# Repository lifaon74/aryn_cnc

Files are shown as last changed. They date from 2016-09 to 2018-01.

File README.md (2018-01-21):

# Aryn CNC

Aryn CNC is a personal project of building a CNC machine for 3D printing, carving, or PCB drilling.
The final should result in a low cost "professional" CNC tool able to work in 50cm x 50cm x 40cm volume (X, Y, Z).

<!---<a href="./main.jpg"><img src="./main.jpg" height="500"></a>-->
Aryn CNC 01 (http://www.youtube.com/watch?v=Y5BFLhbk83g "Aryn CNC 01")

## The goals
* **modular** : easy to add, remove and update parts => it's for me the most important goal.
* **professional** : fast, precise and strong, that's why I chose to use only high quality materials. It increase the price, but he, we want the best no ?
* **'low' cost** : far under the professional market (price estimated around 500$, expensive but not as much as a pro solution). I'm expecting same or better precision.
* **important work volume** : 50cm x 50cm x 40cm (aprox) into a 70cm side cube (you should be able to put it in your car). It's a far better ratio than most of the 3D printer (ex: [Haeckel](http://reprap.org/wiki/Haeckel) 47cm x 47cm x 57cm size for a 20cm x 20cm x 35cm print volume)
* **for makers** : if you have time, are handyman, own a 3D printer (or know someone) and like precision, this CNC is done for you.

## Before your start
* Take care to work as much precise as possible.
* Most of the parts are not available into generic DIY store, you'll need to order them online and/or contact peoples.
* You'll need a **shitload** of screws, nuts and washer : buy them into big pack (1000pcs) and keep them for future projects.
* You'll need a complete set of tools.
* Take care to have enough place (70cm side is big !).

## My Setups
Prusa i3
* 0.2mm layer height
* 30% infill, 50% for some parts which need solidity
* PLA (black, red, and maybe orange)

## Table of Content
1. [x] [Frame](./documentation/frame/frame.md)
2. [x] Axis
	* [x] [X](./documentation/x_axis/x_axis.md)
	* [x] [Y](./documentation/y_axis/y_axis.md)
	* [x] [Z](./documentation/z_axis/z_axis.md) - TODO : plate

3. [x] Tools
	* [x] Extruder
    * [Diamond Head](./documentation/tools/extruder/diamond_head/diamond_head.md) - (in experiment)
	* [x] [Milling](./documentation/tools/milling/milling.md) - (in experiment)

4. [x] Electronic
	* [x] [Power supply](./documentation/power_supply/power_supply.md)
	* [ ] Wiring - TODO
	* [ ] Program and drivers - TODO

**The project is still in progress, some parts may change and it's not my full time job (don't expect it will be finished too fast). This git is here to share my work. Fell free to test, contribute, improve or comment (create issues for that).**

If you want to support the project: 



hit counter

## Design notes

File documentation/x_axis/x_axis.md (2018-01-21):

# X Axis

## BOM
| Quantity | Name |
| :---: | --- |
| 2 | [X carriage](#x-carriage-x-2) |
| 2 | [Motor holder](#motor-holder-x-2) |
| 4 | [Belt tensioner](#belt-tensioner-x-4-2-mirrored) (2 mirrored) |
| 2 | [GT2 Belt](../bom/bom.md) ~80cm |
| 2 | [Aluminum bar](../bom/bom.md) 16mm x 16mm x Xmm (1.5mm thickness) |
| 1 | [Cable chain](#cable-chain) |

### X carriage x 2
#### BOM
##### Bearings
| Quantity | Name |
| :---: | --- |
| 8 | [M3 screw](../bom/bom.md) 16mm |
| 32 | [M3 washer](../bom/bom.md) |
| 8 | [M3 self locking nut](../bom/bom.md) |
| 8 | [623ZZ bearing](../bom/bom.md) |

##### Fixing
| Quantity | Name |
| :---: | --- |
| 8 | [M3 screw](../bom/bom.md) 16mm |
| 8 | [M3 nut](../bom/bom.md) |

#### Print details
* Files: [carriage_bot_x.stl](../../models/XYZ/motors_carriages/carriage/carriage_bot_x.stl), [carriage_top_x.stl](../../models/XYZ/motors_carriages/carriage/carriage_top_x.stl)
* Time: 4h x 2
* Layer height: 0.2mm
* Weight: 50g x 2
* Support: No
* Infill: 50%

#### Build steps
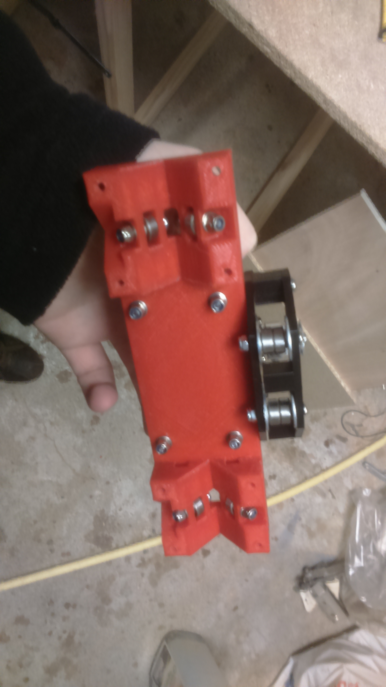
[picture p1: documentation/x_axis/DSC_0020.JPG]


### Motor holder x 2
#### BOM
##### Motor
| Quantity | Name |
| :---: | --- |
| 1 | [Nema 17 motor](../bom/bom.md) |
| 1 | [GT2 pulley](../bom/bom.md) 20 teeth 5mm bore |
| 4 | [M3 screw](../bom/bom.md) 8mm |
| 5 | [M3 screw](../bom/bom.md) 20mm |
| 5 | [M3 nut](../bom/bom.md) |
| 9 | [M3 washer](../bom/bom.md) |
| 2 | [Pulley](../pulley/pulley.md) |

##### Fixing
| Quantity | Name |
| :---: | --- |
| 4 | [M3 screw](../bom/bom.md) 12mm |
| 8 | [M3 washer](../bom/bom.md) |
| 4 | [M3 self locking nut](../bom/bom.md) |

#### Print details
* Files: [motor_block.stl](../../models/XYZ/motors_carriages/motor_block/motor_block.stl), [motor_block_pulley_holder.stl](../../models/XYZ/motors_carriages/motor_block/motor_block_pulley_holder.stl)
* Time: 1h20
* Layer height: 0.2mm
* Weight: 16g
* Support: No

#### Build steps
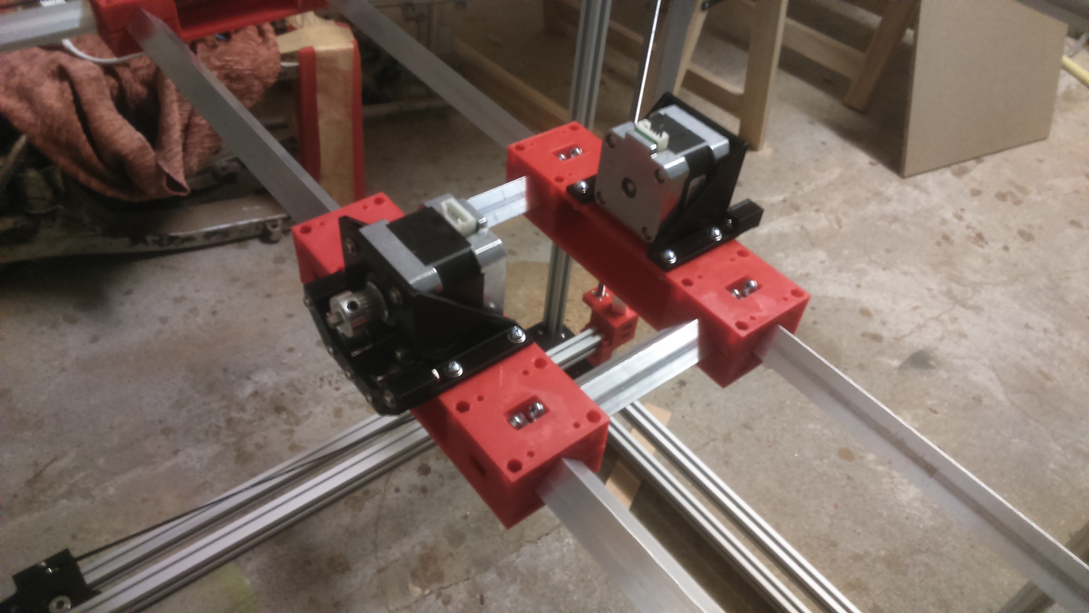
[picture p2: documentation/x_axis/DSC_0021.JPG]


### Belt tensioner x 4 (2 mirrored)
#### Belt grip
##### BOM
| Quantity | Name |
| :---: | --- |
| 2 | [M2 screw](../bom/bom.md) 6~8mm |
| 1 | [M2 screw](../bom/bom.md) 20~25mm |
| 1 | [M2 washer](../bom/bom.md) |
| 3 | [M2 nut](../bom/bom.md) |

##### Print details
* Files: [belt_tensioner_bot.stl](../../models/XYZ/motors_carriages/belt_tensioner/belt_tensioner_bot.stl), [belt_tensioner_top_grip.stl](../../models/XYZ/motors_carriages/belt_tensioner/belt_tensioner_top_grip.stl)
* Time: 10m
* Layer height: 0.2mm
* Weight: 2g
* Support: No

#### Belt grip case
##### BOM
| Quantity | Name |
| :---: | --- |
| 2 | [M3 screw](../bom/bom.md) 30mm |
| 2 | [M3 washer](../bom/bom.md) |
| 2 | [M3 nut](../bom/bom.md) |

##### Print details
* Files: [belt_holder_x_bot.stl](../../models/XYZ/motors_carriages/belt_holder/belt_holder_x_bot.stl), [belt_holder_x_top.stl](../../models/XYZ/motors_carriages/belt_holder/belt_holder_x_top.stl)
* Time: 40m + 5m
* Layer height: 0.2mm
* Weight: 9g + 1.5g
* Support: No
* Infill: 50%

#### Belt grip fix
##### BOM
| Quantity | Name |
| :---: | --- |
| 4 | [M3 screw](../bom/bom.md) 10mm |
| 4 | [M3 washer](../bom/bom.md) |
| 4 | [M3 nut](../bom/bom.md) |

##### Print details
* File: [belt_holder_x_fix.stl](../../models/XYZ/motors_carriages/belt_holder/belt_holder_x_fix.stl)
* Time: 35m
* Layer height: 0.2mm
* Weight: 7.5g
* Support: No

#### Build steps
Take care to have exactly the same length (number of teeth) for both of the belts.

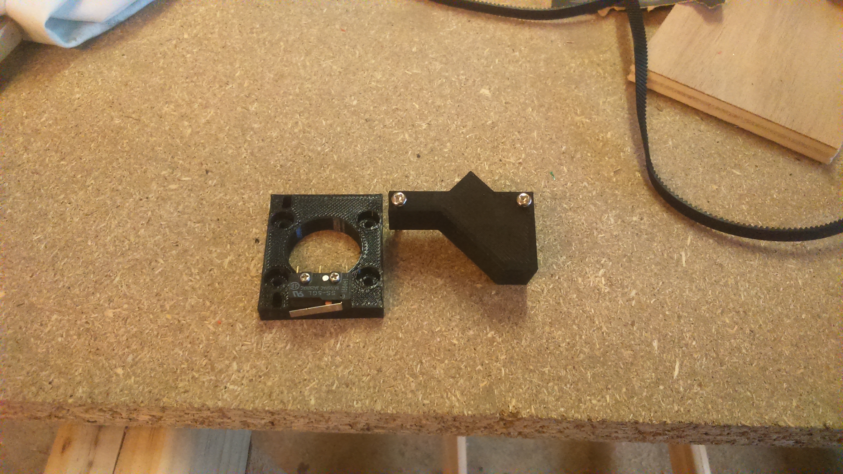
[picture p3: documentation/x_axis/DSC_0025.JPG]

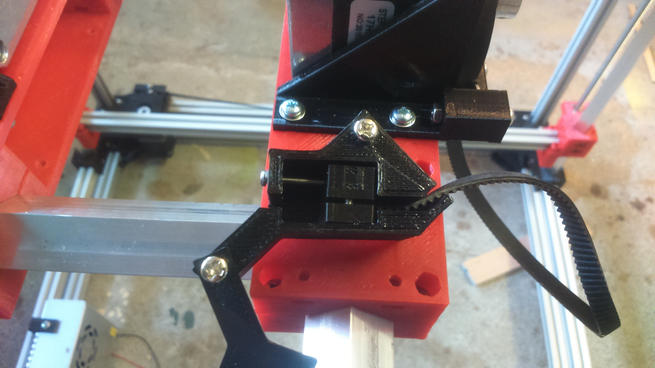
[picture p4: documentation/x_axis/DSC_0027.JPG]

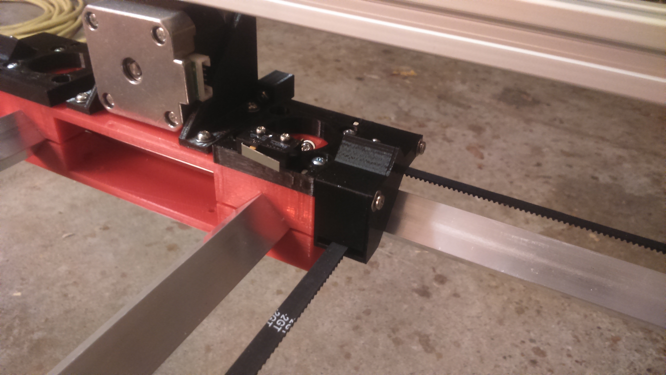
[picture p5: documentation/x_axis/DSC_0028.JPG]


## Final
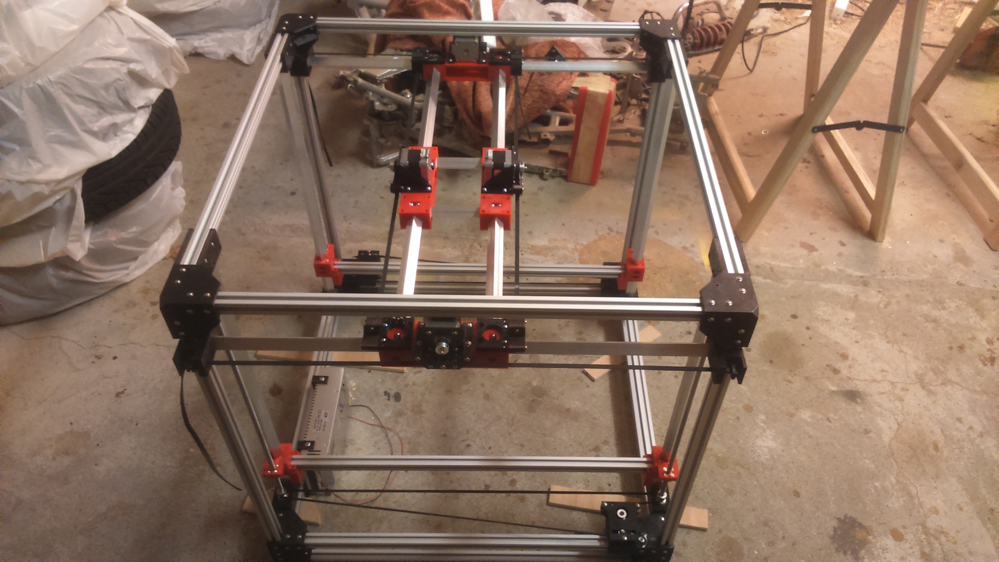
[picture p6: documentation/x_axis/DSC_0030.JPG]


### Cable chain
#### Fix to frame
##### BOM
| Quantity | Name |
| :---: | --- |
| 2 | [M3 screw](../bom/bom.md) 12mm | 
| 2 | [M3 screw](../bom/bom.md) 10mm |
| 4 | [M3 washer](../bom/bom.md) |
| 2 | [M3 nut](../bom/bom.md) |
| 2 | [M3 T nut](../bom/bom.md) |
| 1 | [Cable chain 15x30 (~80cm)](../bom/bom.md) |

##### Print details
* File: [cable_chain_15x30_holder_frame_v2.stl](../../models/XYZ/cable_chain/cable_chain_15x30_holder_frame_v2.stl)
* Time: 1h
* Layer height: 0.2mm
* Weight: 15g
* Support: No

#### Smooth chain slide
##### BOM
| Quantity | Name |
| :---: | --- |
| 2 | [M3 screw](../bom/bom.md) 6mm | 
| 2 | [M3 T nut](../bom/bom.md) |

##### Print details
* File: [corder_3d_smooth_slide.stl](../../models/frame/corder_3d_smooth_slide.stl)
* Time: 40m
* Layer height: 0.1mm
* Weight: 4.5g
* Support: Yes

#### Fix to carriage
##### BOM
| Quantity | Name |
| :---: | --- |
| 2 | [M3 screw](../bom/bom.md) 12mm | 
| 10 | [M3 screw](../bom/bom.md) 10mm |
| 3 | [M3 screw](../bom/bom.md) 30mm | 
| 12 | [M3 washer](../bom/bom.md) |
| 12 | [M3 nut](../bom/bom.md) |

##### Print details
###### Attaches x 2
* File: [cable_chain_15x30_holder_carriage_attach.stl](../../models/XYZ/cable_chain/cable_chain_15x30_holder_carriage_attach.stl)
* Time: 1h25
* Layer height: 0.2mm
* Weight: 18g
* Support: No
* Infill: 10%

###### Bridge
* File: [cable_chain_15x30_holder_carriage_bridge.stl](../../models/XYZ/cable_chain/cable_chain_15x30_holder_carriage_bridge.stl)
* Time: 1h20
* Layer height: 0.2mm
* Weight: 22g
* Support: No

#### Build steps
The cable chain are generally sold by 1m. Disassemble it with a length around 80cm.
Models may evolves or be different than [mine](http://www.ebay.fr/itm/15-x-30mm-1M-Plastic-Drag-Chain-40-Towline-Carrier-Wire-Cable-CNC-Machine-Tool-/322440353260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) (if link no more valid, reference to the image in the bom).
If you don't find the exact same model, you'll probably need to edit the scad files.

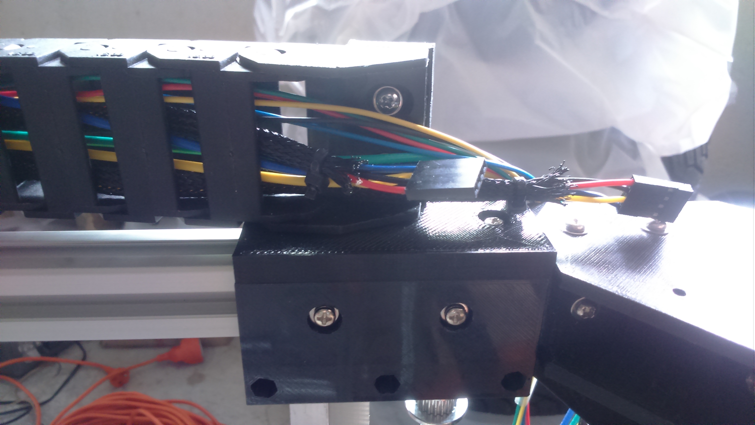
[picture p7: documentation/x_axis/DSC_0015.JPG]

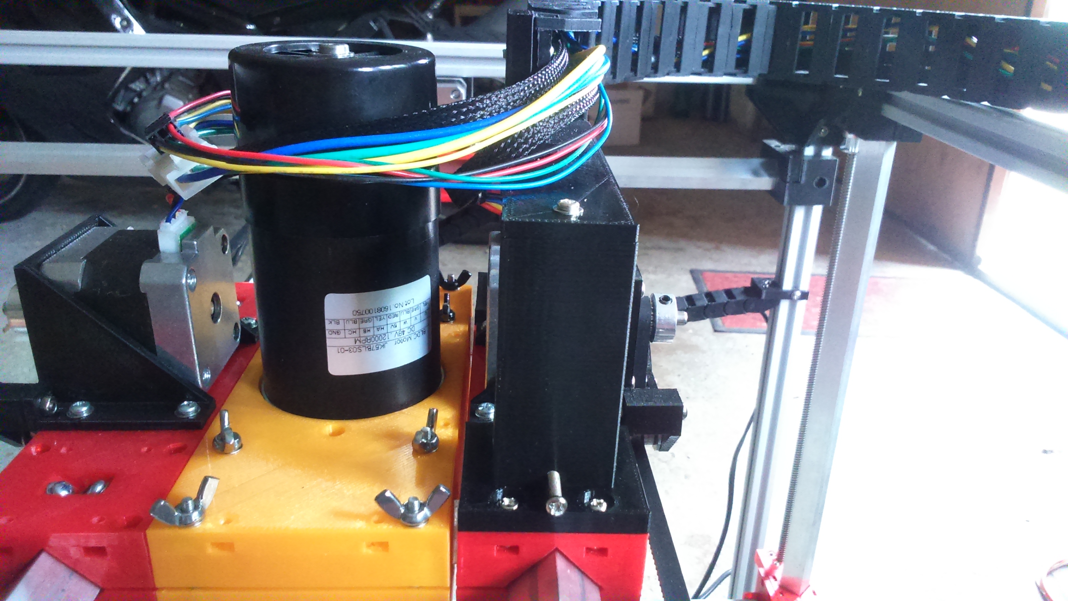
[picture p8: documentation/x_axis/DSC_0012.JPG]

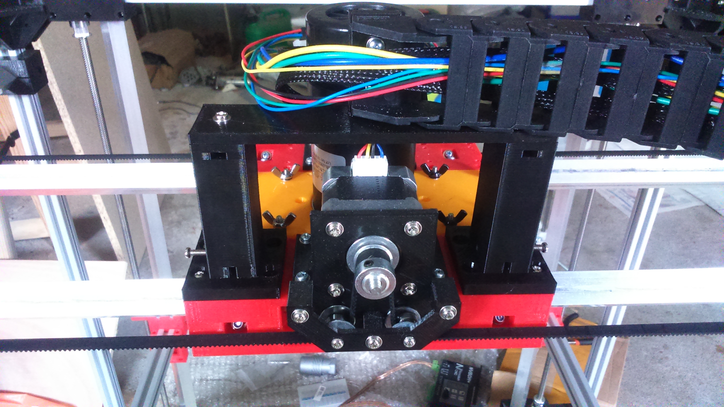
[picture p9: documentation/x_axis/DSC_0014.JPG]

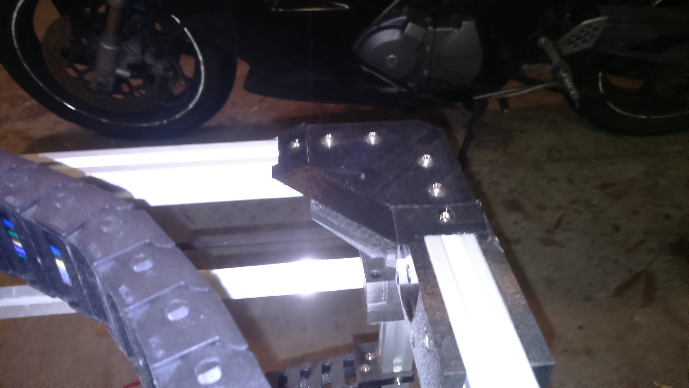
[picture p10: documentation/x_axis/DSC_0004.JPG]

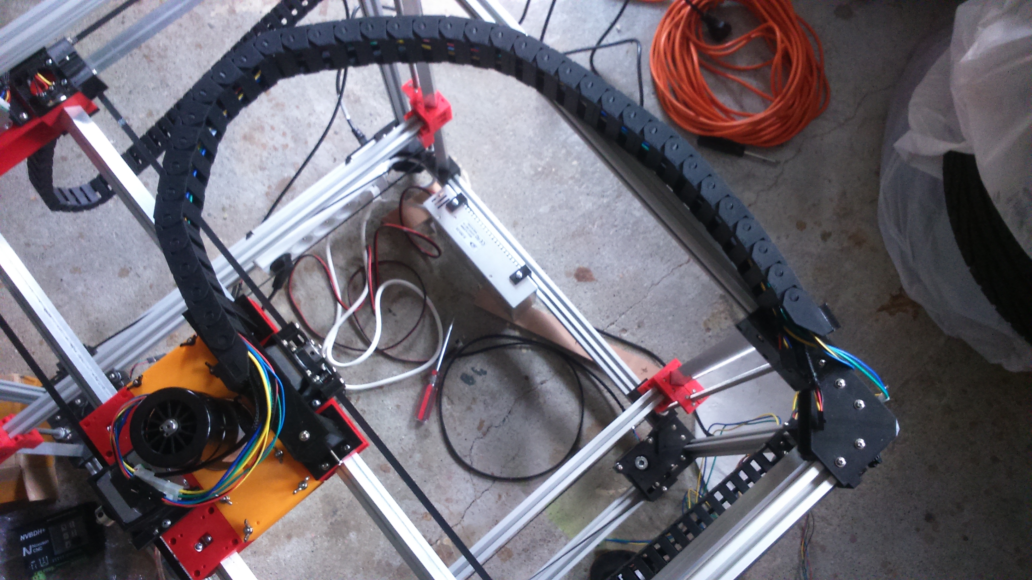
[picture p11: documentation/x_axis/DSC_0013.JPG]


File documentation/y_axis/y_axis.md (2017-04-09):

# Y Axis

## BOM
| Quantity | Name |
| :---: | --- |
| 2 | [Y carriage](#y-carriage-x-2) | 
| 2 | [Motor holder](#motor-holder-x-2) | 
| 4 | [Y frame fix](#frame-fix-x-4-2-mirrored) (2 mirrored) |
| 4 | [Belt tensioner](#belt-tensioner-x-4) |
| 2 | [GT2 Belt](../bom/bom.md) ~80cm |
| 4 | [Aluminum bar](../bom/bom.md) 16mm x 16mm x 649mm (1.5mm thickness) |
| 2 | [Cable chain](#cable-chain-x-2) |

### Y carriage x 2
#### BOM
##### Bearings
| Quantity | Name |
| :---: | --- |
| 8 | [M3 screw](../bom/bom.md) 16mm | 
| 32 | [M3 washer](../bom/bom.md) | 
| 8 | [M3 self locking nut](../bom/bom.md) | 
| 8 | [623ZZ bearing](../bom/bom.md) | 

##### Fixing
| Quantity | Name |
| :---: | --- |
| 8 | [M3 screw](../bom/bom.md) 16mm | 
| 8 | [M3 nut](../bom/bom.md) | 

#### Print details
* Files: [carriage_bot_y.stl](../../models/XYZ/motors_carriages/carriage/carriage_bot_y.stl), [carriage_top_y.stl](../../models/XYZ/motors_carriages/carriage/carriage_top_y.stl)
* Time: 4h x 2
* Layer height: 0.2mm
* Weight: 50g x 2
* Support: No
* Infill: 50%

#### Build steps
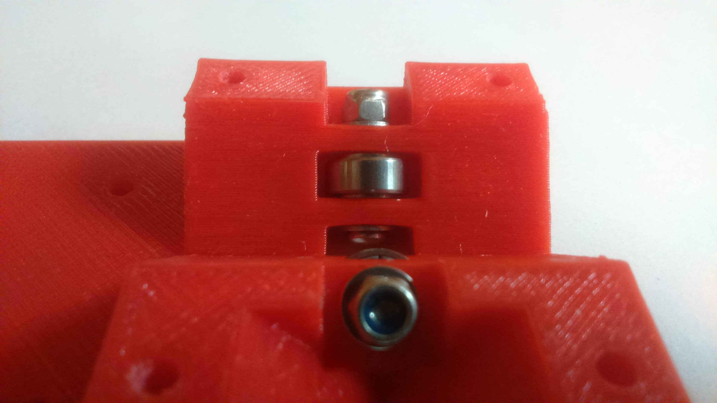
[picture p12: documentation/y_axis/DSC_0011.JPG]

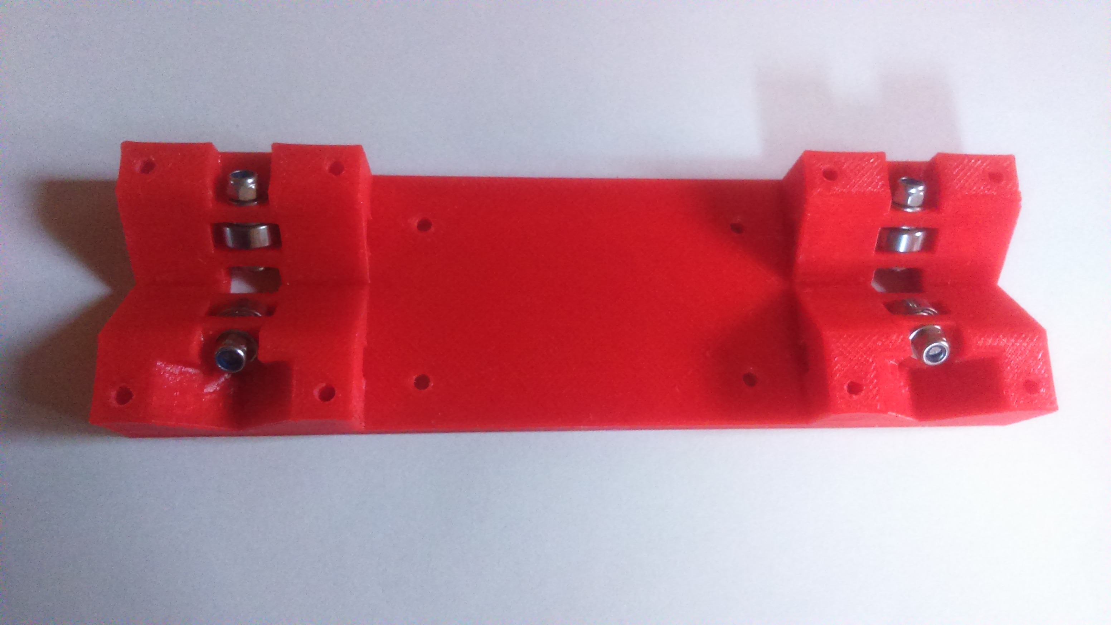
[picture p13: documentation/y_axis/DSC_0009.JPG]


### Motor holder x 2
#### BOM
##### Motor
| Quantity | Name |
| :---: | --- |
| 1 | [Nema 17 motor](../bom/bom.md) | 
| 1 | [GT2 pulley](../bom/bom.md) 20 teeth 5mm bore | 
| 4 | [M3 screw](../bom/bom.md) 8mm | 
| 5 | [M3 screw](../bom/bom.md) 20mm |
| 5 | [M3 nut](../bom/bom.md) |
| 9 | [M3 washer](../bom/bom.md) | 
| 2 | [Pulley](../pulley/pulley.md) | 

##### Fixing
| Quantity | Name |
| :---: | --- |
| 4 | [M3 screw](../bom/bom.md) 12mm | 
| 8 | [M3 washer](../bom/bom.md) | 
| 4 | [M3 self locking nut](../bom/bom.md) | 

#### Print details
* Files: [motor_block.stl](../../models/XYZ/motors_carriages/motor_block/motor_block.stl), [motor_block_pulley_holder.stl](../../models/XYZ/motors_carriages/motor_block/motor_block_pulley_holder.stl)
* Time: 1h20
* Layer height: 0.2mm
* Weight: 16g
* Support: No

#### Build steps
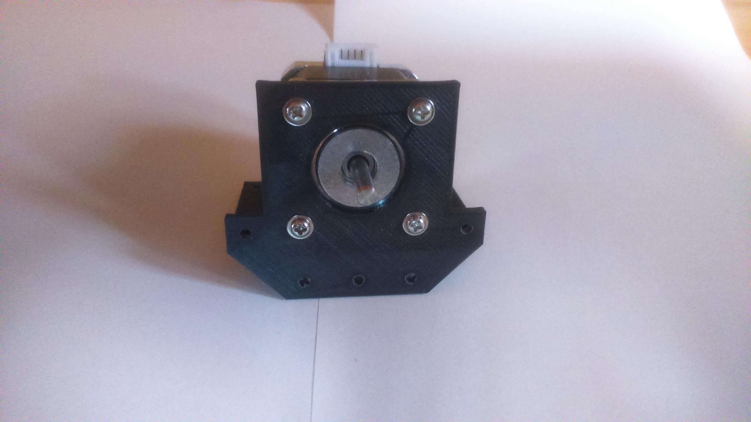
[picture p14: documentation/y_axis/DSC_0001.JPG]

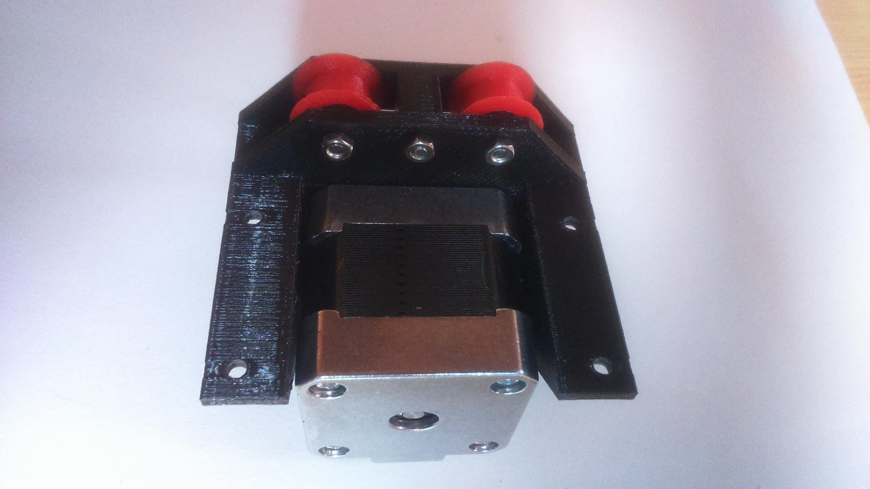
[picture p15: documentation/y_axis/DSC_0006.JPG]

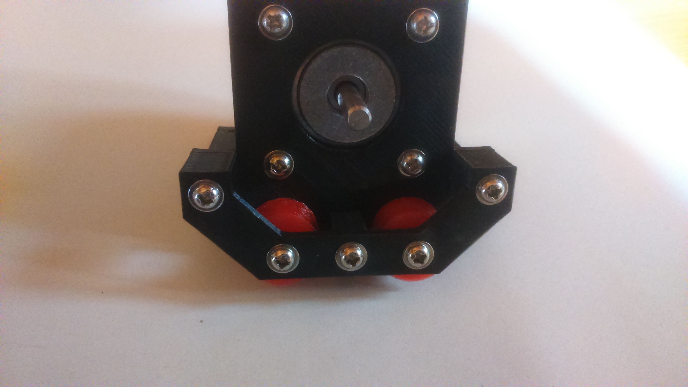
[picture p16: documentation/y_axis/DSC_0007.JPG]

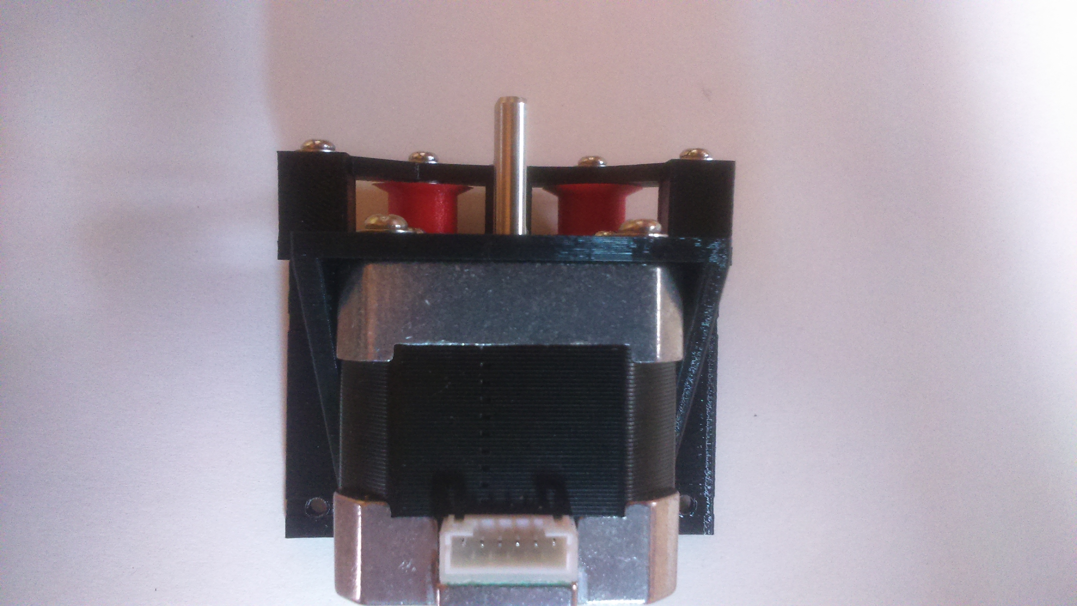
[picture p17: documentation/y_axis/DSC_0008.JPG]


### Frame fix x 4 (2 mirrored)
#### BOM
| Quantity | Name |
| :---: | --- |
| 2 | [M3 screw](../bom/bom.md) 8~10mm | 
| 2 | [M3 screw](../bom/bom.md) 16mm |
| 2 | [M3 washer](../bom/bom.md) |
| 2 | [M3 nut](../bom/bom.md) |
| 2 | [M3 T nut](../bom/bom.md) |

#### Print details
* Files: [motor_block.stl](../../models/XYZ/motors_carriages/rod_fix/rod_fix_bot.stl), [motor_block_pulley_holder.stl](../../models/XYZ/motors_carriages/rod_fix/rod_fix_top.stl)
* Time: 1h30m + 30m
* Layer height: 0.2mm
* Weight: 26g
* Support: No

#### Build steps
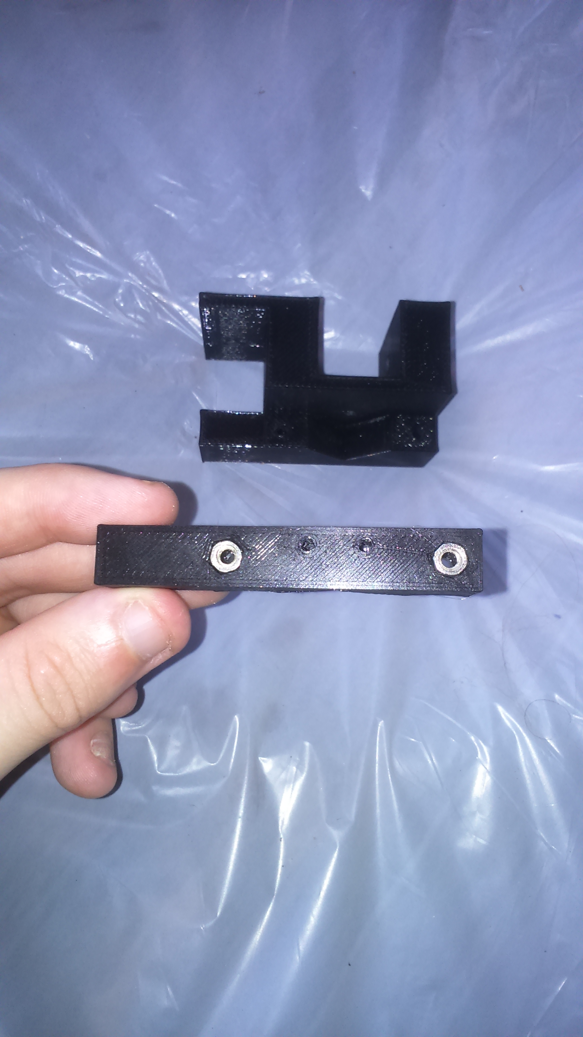
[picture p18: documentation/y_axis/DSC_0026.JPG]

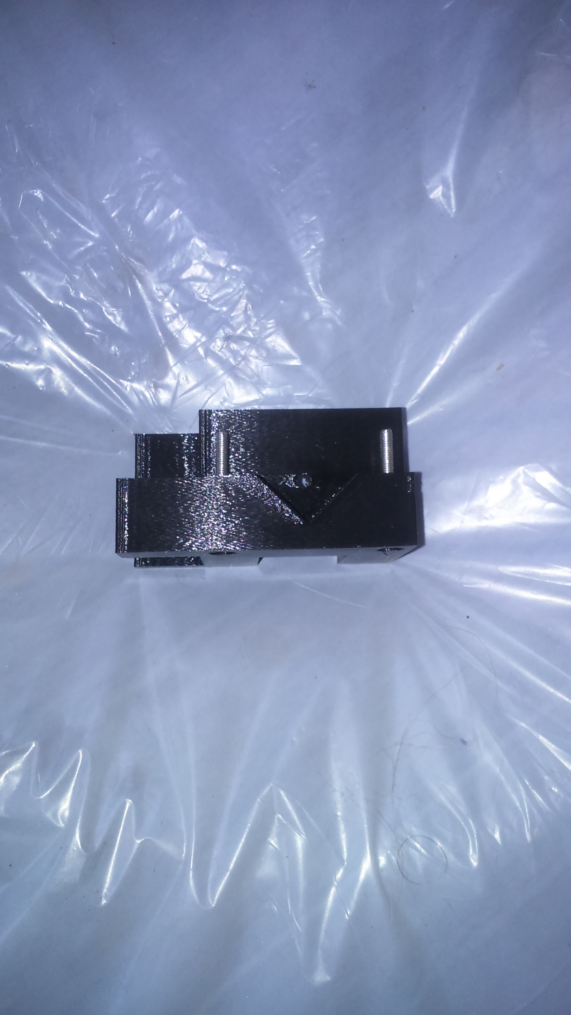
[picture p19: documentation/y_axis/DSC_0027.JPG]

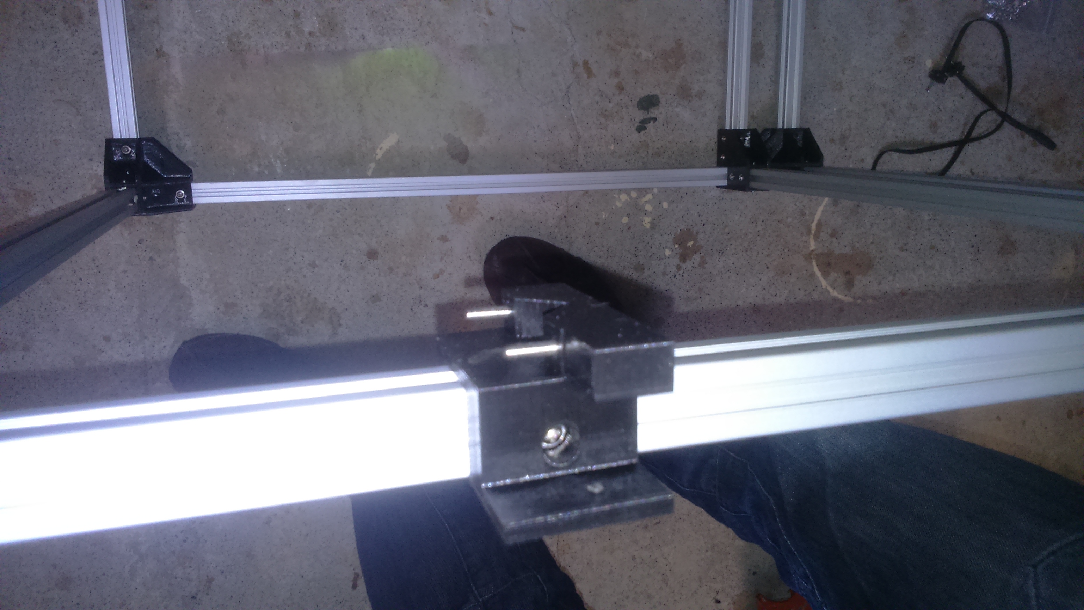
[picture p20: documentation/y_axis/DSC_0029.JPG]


### Belt tensioner x 4
#### BOM
| Quantity | Name |
| :---: | --- |
| 2 | [M2 screw](../bom/bom.md) 6~8mm | 
| 1 | [M2 screw](../bom/bom.md) 25~30mm |
| 1 | [M2 washer](../bom/bom.md) |
| 3 | [M2 nut](../bom/bom.md) |

#### Print details
* Files: [belt_tensioner_bot_grip.stl](../../models/XYZ/motors_carriages/belt_tensioner/belt_tensioner_bot_grip.stl), [belt_tensioner_top.stl](../../models/XYZ/motors_carriages/belt_tensioner/belt_tensioner_top.stl)
* Time: 10m
* Layer height: 0.2mm
* Weight: 2g
* Support: No

#### Build steps
Take care to have exactly the same length (number of teeth) for both of the belts.

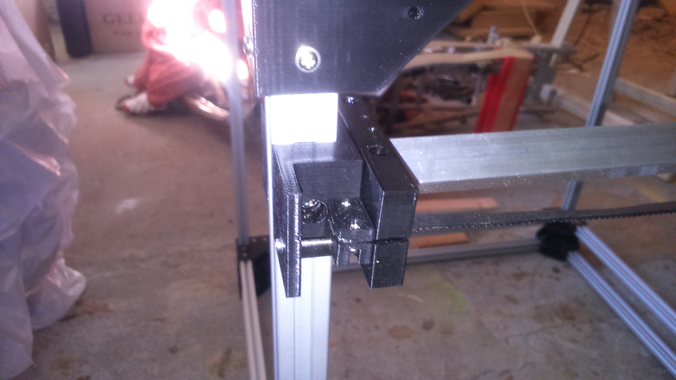
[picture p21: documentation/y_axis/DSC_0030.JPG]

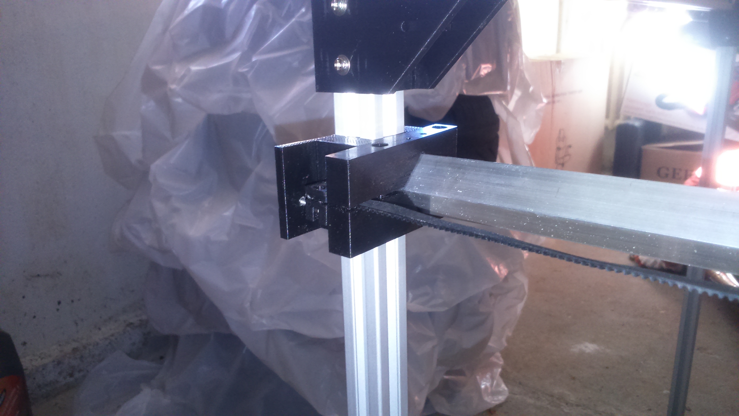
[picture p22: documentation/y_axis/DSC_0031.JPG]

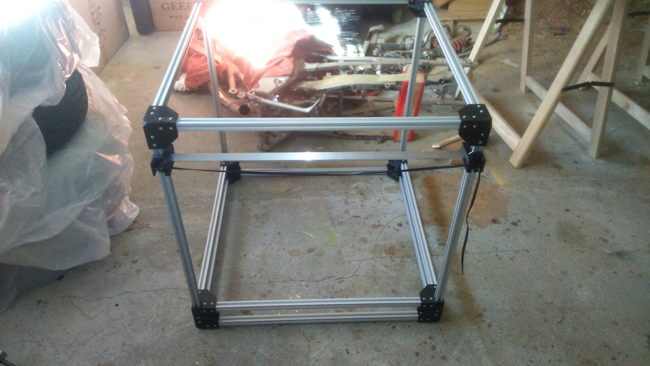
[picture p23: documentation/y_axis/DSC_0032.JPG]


### Assembled
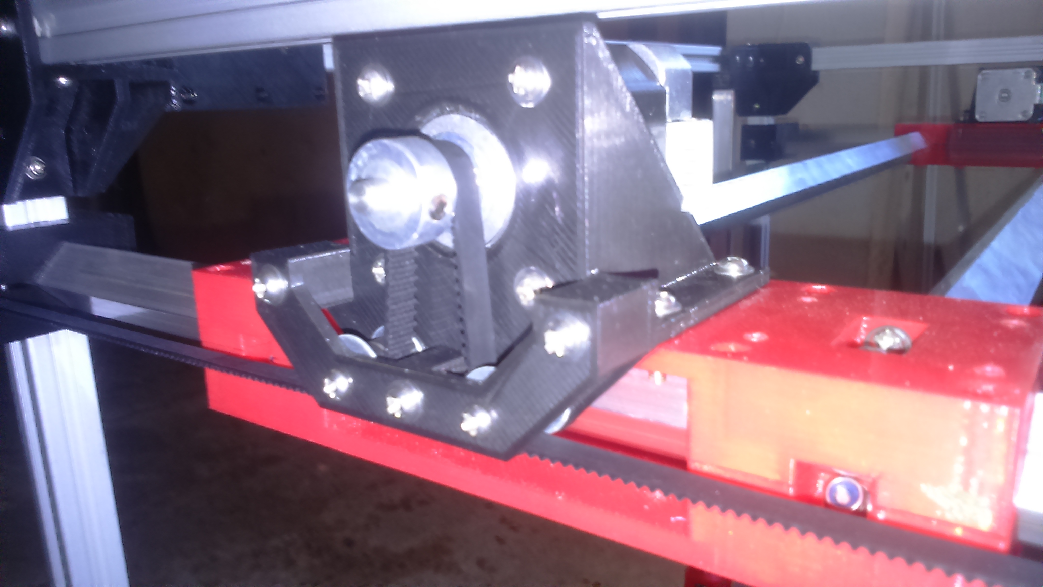
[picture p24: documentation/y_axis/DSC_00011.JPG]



### Cable chain x 2
#### BOM
| Quantity | Name |
| :---: | --- |
| 2 | [M3 screw](../bom/bom.md) 7~8mm | 
| 8 | [M3 screw](../bom/bom.md) 10mm |
| 10 | [M3 washer](../bom/bom.md) |
| 8 | [M3 nut](../bom/bom.md) |
| 2 | [M3 T nut](../bom/bom.md) |
| 1 | [Cable chain 10x20 (70~80cm)](../bom/bom.md) |

#### Print details
* Files: [cable_chain_10x20_holder_frame.stl](../../models/XYZ/cable_chain/cable_chain_10x20_holder_frame.stl),
[cable_chain_10x20_holder_carriage_1.stl](../../models/XYZ/cable_chain/cable_chain_10x20_holder_carriage_1.stl),
[cable_chain_10x20_holder_carriage_2.stl](../../models/XYZ/cable_chain/cable_chain_10x20_holder_carriage_2.stl)
* Time: 15m + 1h
* Layer height: 0.2mm
* Weight: 3.5g + 15g
* Support: Yes

#### Build steps
The cable chain are generally sold by 1m. Disassemble it with a length around 70cm, and you'll probably need to revert one the the ends.
Models may evolves or be different than [mine](http://www.ebay.fr/itm/252523694750?_trksid=p2057872.m2749.l2649&ssPageName=STRK%3AMEBIDX%3AIT) (if link no more valid, reference to the image in the bom).
If you don't find the exact same model, you'll probably need to edit the scad files.




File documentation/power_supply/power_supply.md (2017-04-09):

# Power supply

## BOM
| Quantity | Name |
| :---: | --- |
| 1 | [Power socket](#power-socket) |
| 1 | [Power strip](#power-strip) |
| 1 | [Power supply](#power-supply) |

### Power socket
#### BOM
| Quantity | Name |
| :---: | --- |
| 1 | [Male power socket IEC320](../bom/bom.md) |
| 1 | [Power cord IEC320](../bom/bom.md) |
| - | [Heat Shrink Tubing](../bom/bom.md) ~10cm |
| - | [Wire](../bom/bom.md) ~10cm, 1.5mm^2 |
| 4 | [Crimp Terminal Connector](../bom/bom.md) Female, 6mm width |
| 4 | [M3 screw](../bom/bom.md) 8~10mm |
| 4 | [M3 washer](../bom/bom.md) |
| 4 | [M3 T nut](../bom/bom.md) |

#### Print details
* Files: [power_socket.stl](../../models/electronics/power_supply/power_socket.stl)
* Time: 35min
* Layer height: 0.2mm
* Weight: 13g
* Support: No
* Infill: 50%

#### Build steps
Take care to properly insulate the metal contacts to avoid electrocution !


### Power strip
##### BOM
| Quantity | Name |
| :---: | --- |
| 1 | [Power strip](../bom/bom.md) 5 outlets |
| 2 | [Power strip fix](#power-strip-fix-x-2) |

#### Power strip fix x 2
##### BOM
| Quantity | Name |
| :---: | --- |
| 2 | [M3 screw](../bom/bom.md) 8~10mm |
| 2 | [M3 washer](../bom/bom.md) |
| 1 | [M3 self locking nut](../bom/bom.md) |
| 1 | [M3 T nut](../bom/bom.md) |

##### Print details
* Files: [power_strip_fix.stl](../../models/electronics/power_supply/power_strip_fix.stl)
* Time: 25min
* Layer height: 0.2mm
* Weight: 3g
* Support: No

#### Build steps
Drill two holes into the power strip, then fix the printed part to it with a screw, a washer and a self-locking nut. Finally, fix it to the frame.



### Power supply
##### BOM
| Quantity | Name |
| :---: | --- |
| 1 | [Power supply](../bom/bom.md) 24V 15A |
| 1 | [Male plug](../bom/bom.md) ~20cm |
| - | [Wire](../bom/bom.md) 20~50cm, 1.5mm^2 |
| 2 | [Power supply fix](#power-supply-fix-x-2) |

#### Power supply fix x 2
##### BOM
| Quantity | Name |
| :---: | --- |
| 2 | [M3 screw](../bom/bom.md) 8~10mm |
| 2 | [M3 washer](../bom/bom.md) |
| 2 | [M3 T nut](../bom/bom.md) |
| 2 | [M4 screw](../bom/bom.md) 6~7mm |

##### Print details
* Files: [power_supply_fix.stl](../../models/electronics/power_supply/power_supply_fix.stl)
* Time: 55m
* Layer height: 0.2mm
* Weight: 11g
* Support: No

#### Build steps
For driving the steppers, I recommand a 24V 15A power supply.
For the spindler (CNC mode) I recommand a second 48V 10A power supply.



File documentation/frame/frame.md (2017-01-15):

# Frame

## BOM
| Quantity | Name |
| :---: | --- |
| 4 | [Top corner](#top-corners-x-4) | 
| 4 | [Bottom corner](#bottom-corners-x-4) | 
| 4 | [Foot](#foot-x-4) (optional) |
| 4 | [Horizontal corner](#horizontal-corners-x-4) |
| 12 | [Extruded aluminum](../bom/bom.md) 20mm x 20mm x 650mm |

### Top corner x 4
#### BOM
| Quantity | Name |
| :---: | --- |
| 18 | [M3 screw](../bom/bom.md) 8~10mm | 
| 18 | [M3 washer](../bom/bom.md) | 
| 18 | [M3 T nut](../bom/bom.md) | 

#### Print details
* File: [corner_3d_top.stl](../../models/frame/corner_3d_top.stl)
* Time: 6h
* Layer height: 0.2mm
* Weight: 72g
* Support: Yes
* Infill: 50%
 
### Bottom corner x 4
#### BOM
| Quantity | Name |
| :---: | --- |
| 18 | [M3 screw](../bom/bom.md) 8~10mm | 
| 18 | [M3 washer](../bom/bom.md) | 
| 18 | [M3 T nut](../bom/bom.md) | 
| 1 | [M6 nut](../bom/bom.md) | 

#### Print details
* File: [corner_3d_bot.stl](../../models/frame/corner_3d_bot.stl)
* Time: 6h
* Layer height: 0.2mm
* Weight: 72g
* Support: Yes
* Infill: 50%

### Foot x 4
#### BOM
| Quantity | Name |
| :---: | --- |
| 1 | [M6 screw](../bom/bom.md) |
| 1 | [M6 nut](../bom/bom.md) |

#### Print details
* File: [foot.stl](../../models/frame/foot.stl)
* Time: 25min
* Layer height: 0.2mm
* Weight: 4.5g
* Support: NO
* Infill: 50%

### Horizontal corner x 4
#### BOM
| Quantity | Name |
| :---: | --- |
| 16 | [M3 screw](../bom/bom.md) 8~10mm | 
| 16 | [M3 washer](../bom/bom.md) | 
| 16 | [M3 T nut](../bom/bom.md) | 

#### Print details
* File: [corner_2d.stl](../../models/frame/corner_2d.stl)
* Time: 3h
* Layer height: 0.2mm
* Weight: 48g
* Support: Yes
* Infill: 50%

## Build steps
When you'll cut the extruded aluminum bar, take care to be really precise else you could have some problems while building the frame.












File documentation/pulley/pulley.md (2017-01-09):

# Pulley

## Type 1
Full metal : stronger and more regular than type 2. I finally chosed this.
### BOM
| Quantity | Name |
| :---: | --- |
| 2 | [M3 washer](../bom/bom.md) | 
| 2 | [M3/M4 washer 14mm](../bom/bom.md) | 
| 2 | [623ZZ bearing](../bom/bom.md) | 



## Type 2
The problem of this pulley : the print part is not totally perfect (a circle with maybe +-0.05mm) and result in little imperfections.
The advantage: the belt can't rub.

### BOM
| Quantity | Name |
| :---: | --- |
| 2 | [M3 washer](../bom/bom.md) | 
| 2 | [M3 nut](../bom/bom.md) | 
| 1 | [623ZZ bearing](../bom/bom.md) | 

#### Print details
* File: [belt_pulley.stl](../../models/XYZ/motors_carriages/belt_pulley.stl)
* Time: 5m
* Layer height: 0.2mm
* Weight: 1g
* Support: No



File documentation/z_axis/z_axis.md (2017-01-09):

# Z Axis

- TODO link table of contents
- TODO build plate !

## BOM
| Quantity | Name |
| :---: | --- |
| 4 | [Z carriage](#) | 
| 2 | [Motor holder](#) | 
| 2 | [Belt tensioner](#) | 
| 8 | [Z frame fix](#) (4 mirrored) |
| 2 | [GT2 Belt](../bom/bom.md) loop 1524mm |

### Z carriage x 4
#### BOM
##### Bearings
| Quantity | Name |
| :---: | --- |
| 4 | [M3 screw](../bom/bom.md) 16mm | 
| 16 | [M3 washer](../bom/bom.md) | 
| 4 | [M3 self locking nut](../bom/bom.md) | 
| 4 | [623ZZ bearing](../bom/bom.md) | 

##### Lead nut
| Quantity | Name |
| :---: | --- |
| 4 | [M3 screw](../bom/bom.md) 16mm | 
| 4 | [M3 nut](../bom/bom.md) | 
| 1 | [Threaded rod lead nut](../bom/bom.md) | 

##### Fixing
| Quantity | Name |
| :---: | --- |
| 4 | [M3 screw](../bom/bom.md) 16mm | 
| 4 | [M3 nut](../bom/bom.md) | 

#### Print details
* Files: [carriage_z_back.stl](../../models/XYZ/Z/carriage/carriage_z_back.stl), [carriage_z_front.stl](../../models/XYZ/Z/carriage/carriage_z_front.stl)
* Time: 2h x 2
* Layer height: 0.2mm
* Weight: 13g x 2
* Support: No
* Infill: 50%

#### Build steps




### Motor holder x 2
#### BOM
##### Motor
###### High torque (recommended, can lift ~16kg)
| Quantity | Name |
| :---: | --- |
| 1 | [Nema 17 with gearbox](../bom/bom.md) | 
| 1 | [GT2 pulley](../bom/bom.md) 20 teeth 8mm bore | 
| 4 | [M3 screw](../bom/bom.md) 35mm | 
| 4 | [M3 washer](../bom/bom.md) | 

###### Low torque (alternative, can lift ~4kg)
| Quantity | Name |
| :---: | --- |
| 1 | [Nema 17](../bom/bom.md) | 
| 1 | [GT2 pulley](../bom/bom.md) 20 teeth 5mm bore | 
| 4 | [M3 screw](../bom/bom.md) 8mm | 
| 4 | [M3 washer](../bom/bom.md) | 

##### Fixing
| Quantity | Name |
| :---: | --- |
| 4 | [M3 screw](../bom/bom.md) 8~10mm | 
| 4 | [M3 washer](../bom/bom.md) | 
| 4 | [M3 self locking nut](../bom/bom.md) | 

#### Print details
##### Motor block
* File: [motor_block.stl](../../models/XYZ/Z/motor_block/motor_block.stl)
* Time: 1h50
* Layer height: 0.2mm
* Weight: 22g
* Support: No

##### Gearbox adatper (high torque)
* File: [motor_gearbox_adapter.stl](../../models/XYZ/Z/motor_block/motor_gearbox_adapter.stl)
* Time: 40m
* Layer height: 0.2mm
* Weight: 4g
* Support: No

#### Build steps



### Belt tensioner x 2
#### BOM
| Quantity | Name |
| :---: | --- |
| 3 | [Pulley](../pulley/pulley.md) |
| 4 | [M3 screw](../bom/bom.md) 30mm | 
| 1 | [M3 screw](../bom/bom.md) 20mm | 
| 6 | [M3 washer](../bom/bom.md) | 
| 7 | [M3 nut](../bom/bom.md) | 
| 1 | [M3 self locking nut](../bom/bom.md) | 
| 1 | [M3 butterfly nut](../bom/bom.md) | 

#### Print details
* File: [motor_block_pulley_holder_bot.stl](../../models/XYZ/Z/motor_block/motor_block_pulley_holder_bot.stl), [motor_block_pulley_holder_top.stl](../../models/XYZ/Z/motor_block/motor_block_pulley_holder_top.stl), [pulley_holder.stl](../../models/XYZ/Z/motor_block/pulley_holder.stl)
* Time: 40min + 40min + 5min
* Layer height: 0.2mm
* Weight: 7g + 7g + 1g
* Support: No

#### Build steps




Take time to adjust the space beetween this part and the motor bloc. Maybe you'll need to add more washes.





### Frame fix x 8 (4 mirrored)

#### BOM
##### For a pair of fixations (top and bottom)
| Quantity | Name |
| :---: | --- |
| 1 | [Aluminum bar](../bom/bom.md) 16mm x 16mm x Xmm (1.5mm thickness) |
| 1 | [Threaded rod](../bom/bom.md) 8mm x 580mm |

##### For individual fixation
| Quantity | Name |
| :---: | --- |
| 4 | [M3 screw](../bom/bom.md) 8~10mm or 35mm |
| 3 | [M3 screw](../bom/bom.md) 16mm |
| 4 | [M3 washer](../bom/bom.md) |
| 3 | [M3 nut](../bom/bom.md) |
| 4 | [M3 T nut](../bom/bom.md) |
| 1 | [608ZZ bearing](../bom/bom.md) |
| 1 | [Thrust bearing 8mm](../bom/bom.md) |
| 1 | [GT2 pulley (20 teeth 8mm bore)](../bom/bom.md) |

#### Print details
* Files: [rod_fix_z_bot.stl](../../models/XYZ/Z/rod_fix_z/rod_fix_z_bot.stl), [rod_fix_z_top.stl](../../models/XYZ/Z/rod_fix_z/rod_fix_z_top.stl)
* Time: 1h30 + 40m
* Layer height: 0.2mm
* Weight: 32g
* Support: No
* Infill: 50%

#### Build steps




##### Infos
* The top is the same as the bottom (thrust bearing and GT2 pulley) except that the belt goes only on the bottom.
* It's not visible on the pictures, but there's too a GT2 pulley on the top. The purpose is to limit the movements of the rod on the Z axis.

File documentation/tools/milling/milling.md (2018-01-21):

# Spindler

## BOM
| Quantity | Name |
| :---: | --- |
| 2 | [Tool Fix](#tool-fix) | 
| 1 | [Spindler Holder](#spindler-holder) | 

### Tool Fix x 2
#### BOM
| Quantity | Name |
| :---: | --- |
| 8 | [M3 screw](../../bom/bom.md) 35mm | 
| 8 | [M3 self locking nut](../../bom/bom.md) | 
| 8 | [M3 washer](../../bom/bom.md) | 
| 8 | [M3 butterfly nut](../../bom/bom.md) | 

#### Print details
* Files: [tool_base_bot.stl](../../../models/tools/tool_base_bot.stl)
* Time: 1h20
* Layer height: 0.2mm
* Weight: 25g
* Support: No
* Infill: 25%

#### Build steps



**[INFO]** Springs ([Spring 4.8mm](../bom/bom.md)) can be put between the plastic part and the butterfly nuts.

### Spindler Holder
#### BOM
| Quantity | Name |
| :---: | --- |
| 4 | [M4 screw](../../bom/bom.md) 20mm | 
| 4 | [M4 washer](../../bom/bom.md) | 

#### Print details
* Files: [spindler_laser_diode.stl](../../../models/tools/spindler/spindler_laser_diode.stl)
* Time: 6h30
* Layer height: 0.2mm
* Weight: 100g
* Support: Yes
* Infill: 25%

#### Build steps



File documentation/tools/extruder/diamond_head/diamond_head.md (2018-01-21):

# Extruder: Diamond head (3 pipes)

## BOM
| Quantity | Name |
| :---: | --- |
| 2 | [Tool Fix](#tool-fix) | 
| 1 | [Diamond HotEnd Holder](#diamond-hotend-holder) | 
| 1 | [BL Touch - optional](#bl-touch) | 
| 1 | [Radial Fan - optional](#radial-fan) | 

### Tool Fix x 2
[Same part as milling](../../milling/milling.md)

### Diamond HotEnd Holder
#### BOM
| Quantity | Name |
| :---: | --- |
| 1 | [Diamond HotEnd 3 pipes](../../../bom/bom.md) | 
| 1 | [Fan 40mm](../../../bom/bom.md) | 
| 3 | [M3 screw](../../../bom/bom.md) 14~16mm | 
| 4 | [M3 screw](../../../bom/bom.md) 12~13mm | 
| 7 | [M3 nut](../../../bom/bom.md) | 

#### Print details
* Files: [diamond_hotend_base.stl](../../../../models/tools/hotend/diamond_hotend_base.stl), [diamond_hotend_top_cover.stl](../../../../models/tools/hotend/diamond_hotend_top_cover.stl)
* Time: 6h + 1h10
* Layer height: 0.2mm
* Weight: 72g + 13g
* Support: Yes
* Infill: 25%

#### Build steps




### BL Touch
#### BOM
| Quantity | Name |
| :---: | --- |
| 1 | [BL Touch](../../../bom/bom.md) | 
| 4 | [M3 screw](../../../bom/bom.md) 6mm | 
| 1 | [M3 screw](../../../bom/bom.md) 30mm | 
| 5 | [M3 nut](../../../bom/bom.md) | 
| 2 | [M3 self locking nut](../../../bom/bom.md) | 

#### Print details
* Files: [diamond_hot_end_bltouch_holder.stl](../../../../models/tools/hotend/diamond_hot_end_bltouch_holder.stl), [diamond_hot_end_bltouch_fix_top.stl](../../../../models/tools/hotend/diamond_hot_end_bltouch_fix_top.stl)
* Time: 10m + 7m
* Layer height: 0.2mm
* Weight: 1.5g + 1.3g
* Support: No

#### Build steps



### Radial Fan 
#### BOM
| Quantity | Name |
| :---: | --- |
| 1 | [Radial fan 50mm](../../../bom/bom.md) | 
| 1 | [M3 screw](../../../bom/bom.md) 8mm | 
| 2 | [M3 screw](../../../bom/bom.md) 20mm | 
| 2 | [M3 nut](../../../bom/bom.md) | 

#### Print details
* Files: [diamond_hot_end_fan_holder.stl](../../../../models/tools/hotend/diamond_hot_end_fan_holder.stl)
* Time: 8m
* Layer height: 0.2mm
* Weight: 2g
* Support: No

#### Build steps


-- TODO : air blower on plastic

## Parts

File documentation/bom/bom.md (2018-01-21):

# BOM

| Name | Image |
| :---: | --- |
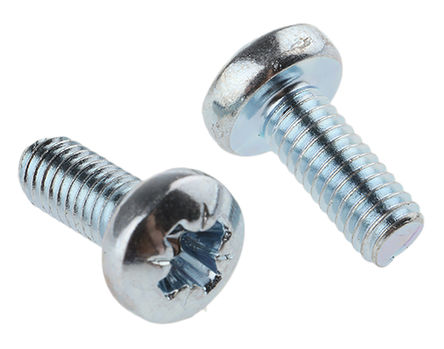
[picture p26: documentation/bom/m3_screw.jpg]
| M3 screw |  | 
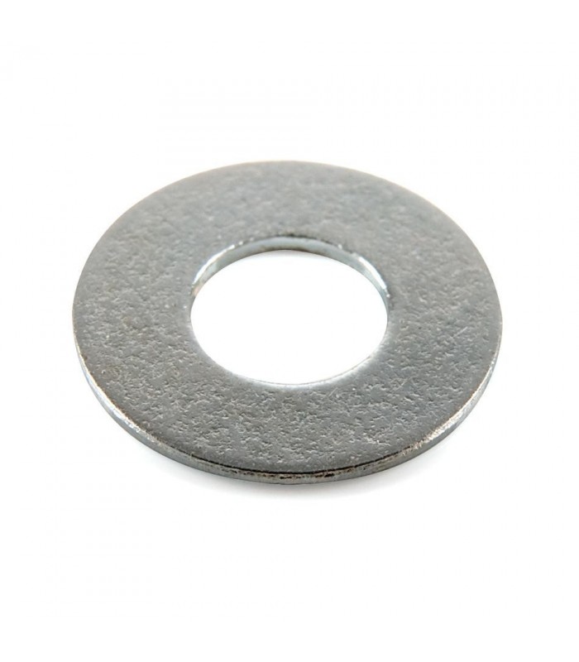
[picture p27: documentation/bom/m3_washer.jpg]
| M3 washer |  | 
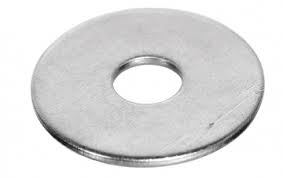
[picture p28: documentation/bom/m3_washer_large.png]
| M3 washer large |  | 
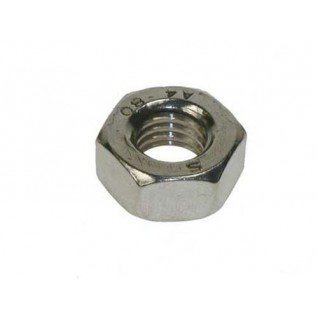
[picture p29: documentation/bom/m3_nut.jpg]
| M3 nut |  | 
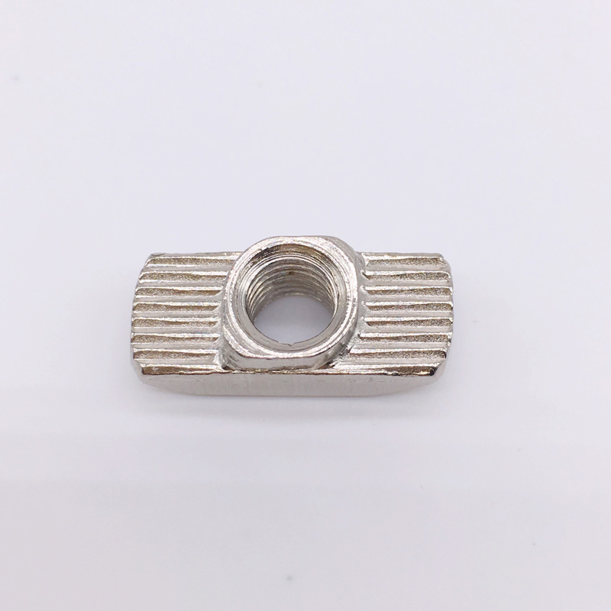
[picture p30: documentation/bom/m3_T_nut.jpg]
| M3 T nut |  | 
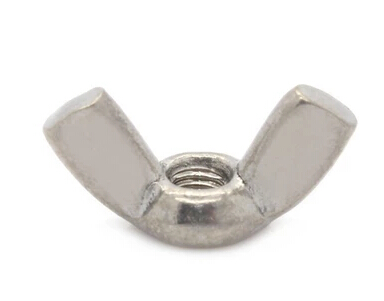
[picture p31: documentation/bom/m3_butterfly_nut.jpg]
| M3 butterfly nut |  | 
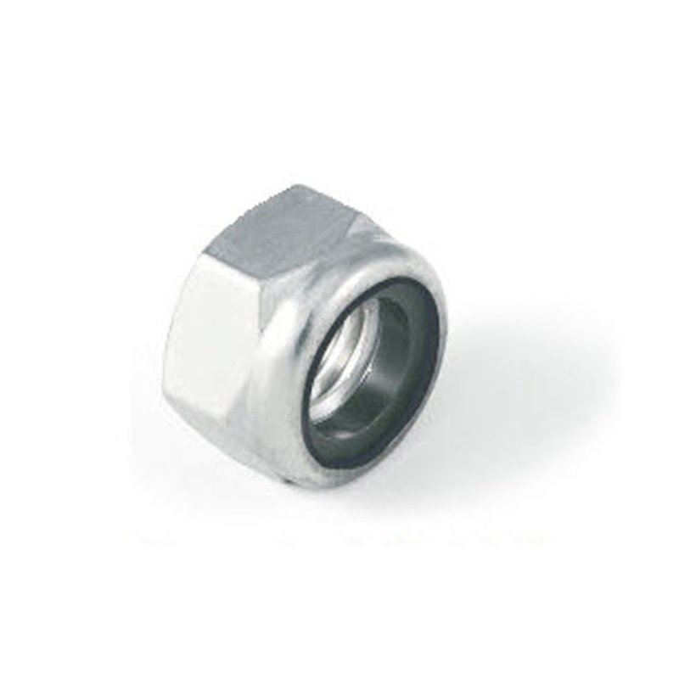
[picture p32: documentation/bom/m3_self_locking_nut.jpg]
| M3 self locking nut |  | 
| | | 
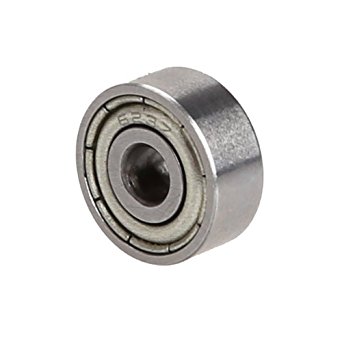
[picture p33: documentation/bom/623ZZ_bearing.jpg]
| 623ZZ bearing |  |
| 608ZZ bearing |  |
| Thrust bearing 8mm |  | 
| | |
| M6 screw |  |
| M6 nut |  |
| | |
| Extruded aluminum |  | 
| Aluminum bar . 16mm x 16mm x Xmm (1.5mm thickness) |  | 
| | | 
| Nema 17 (17HS4401) |  | 
| Nema 17 with gearbox (17HS15-1684S-PG5) |  | 
| GT2 pulley (20 teeth 5mm bore)|  | 
| GT2 pulley (20 teeth 8mm bore)|  | 
| GT2 Belt |  | 
| GT2 Belt 1524mm |  | 
| | |
| Threaded rod (THSL-600-8D) + Lead Nut 8mm |  |
| | |
| Switch (SS-5GL) |  | 
| | |
| Male power socket IEC320  |  |
| Heat Shrink Tubing  |  |
| Wire  |  |
| Crimp Terminal Connector  |  |
| Male plug |  |
| Power strip |  |
| Power supply |  |
| | |
| Cable chain 10x20 |  |
| Cable chain 15x30 |  |
| | |
| Spindler (DC brushless motor 48V, with er8) |  |
| DC brushless motor driver (NVBDH+) |  |
| | |
| Diamond HotEnd 3 pipes |  |
| | |
| Fan 40mm |  |
| Radial fan 50mm |  |
| | |
| BL Touch |  |
| | |
| Spring 4.8mm |  |

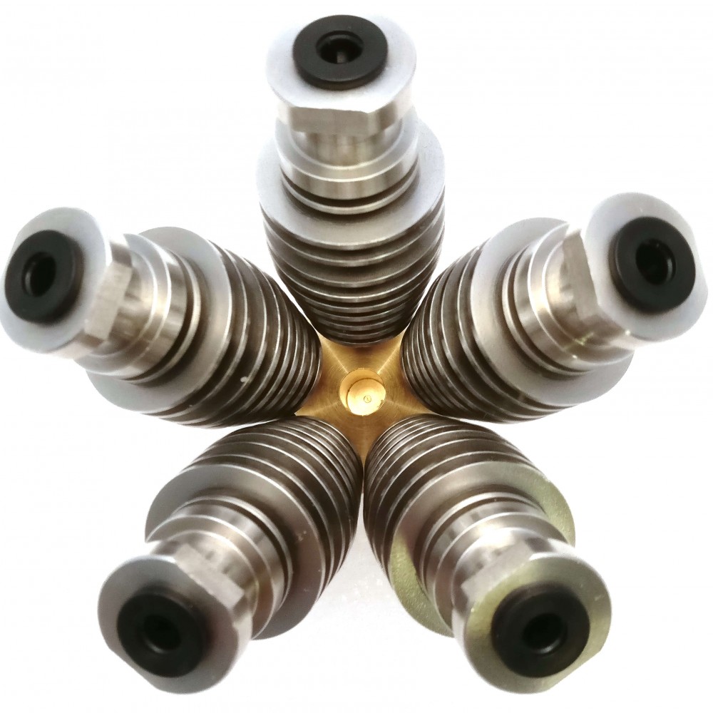
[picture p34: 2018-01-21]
documentation/bom/diamond_hotend_5.jpg

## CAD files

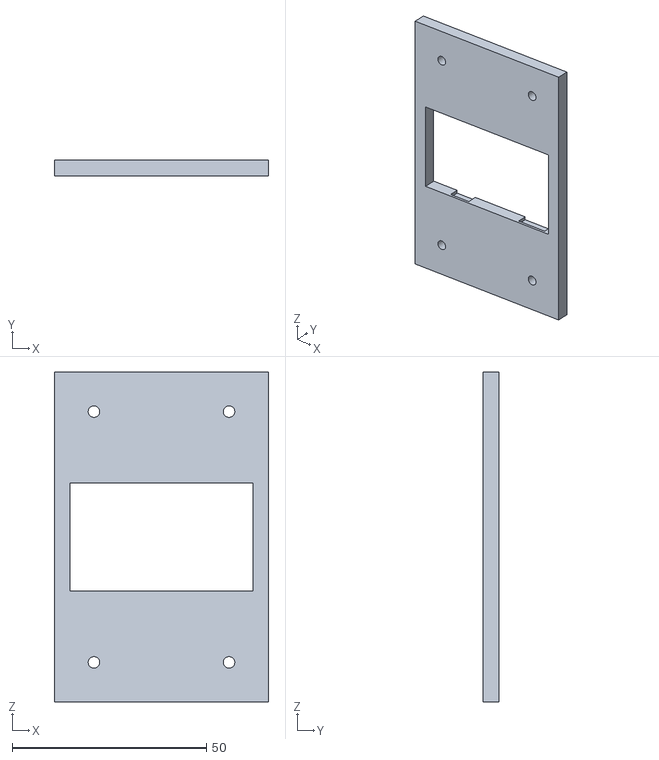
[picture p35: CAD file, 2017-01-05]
models/electronics/power_supply/power_socket.stl
55.2 x 4.00 x 85.0

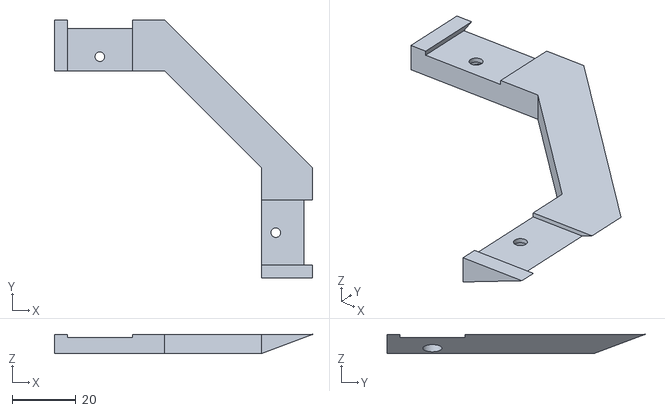
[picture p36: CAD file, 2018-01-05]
models/frame/corder_3d_smooth_slide.stl
80.8 x 80.8 x 6.00

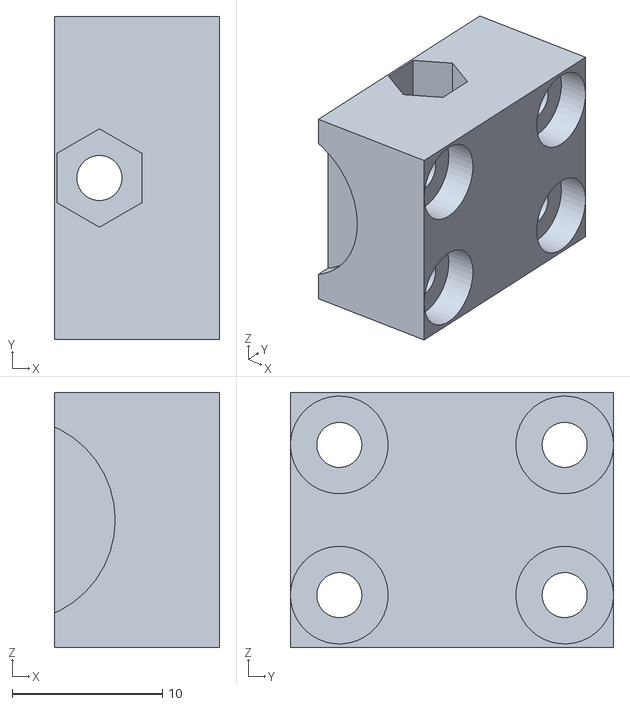
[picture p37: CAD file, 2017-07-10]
models/tools/extruder/push_gear_part.stl
11.0 x 21.5 x 17.0

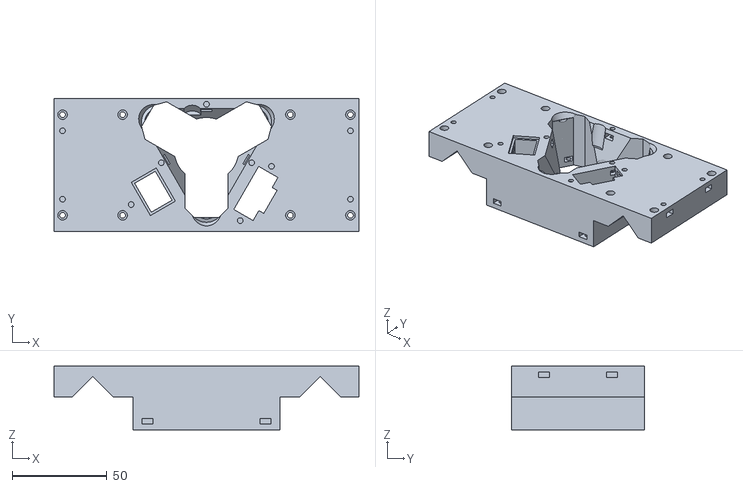
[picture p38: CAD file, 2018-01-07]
models/tools/hotend/diamond_hotend_base.stl
160.6 x 70.0 x 33.5

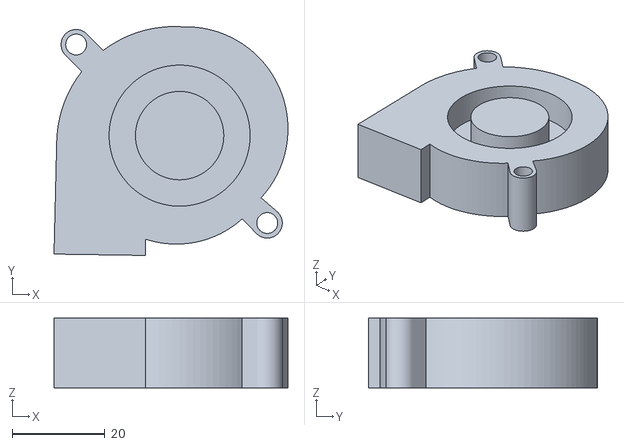
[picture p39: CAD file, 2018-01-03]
models/tools/models/radial_fan_50mm.stl
50.5 x 49.4 x 15.0

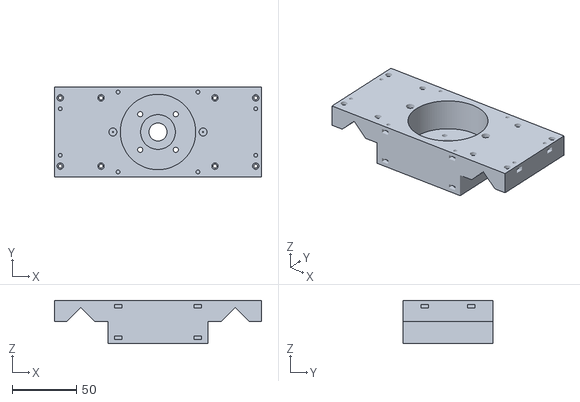
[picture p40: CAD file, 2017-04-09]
models/tools/spindler/spindler_laser_diode.stl
160.6 x 70.0 x 33.5

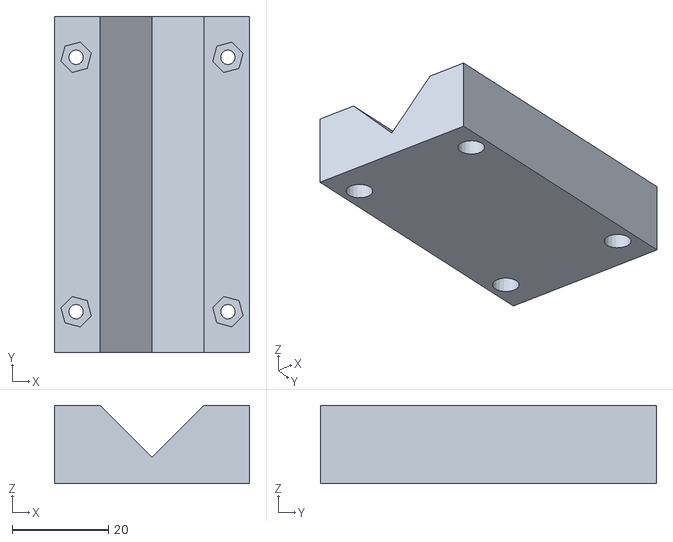
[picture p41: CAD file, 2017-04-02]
models/tools/tool_base_bot.stl
40.6 x 70.0 x 16.3

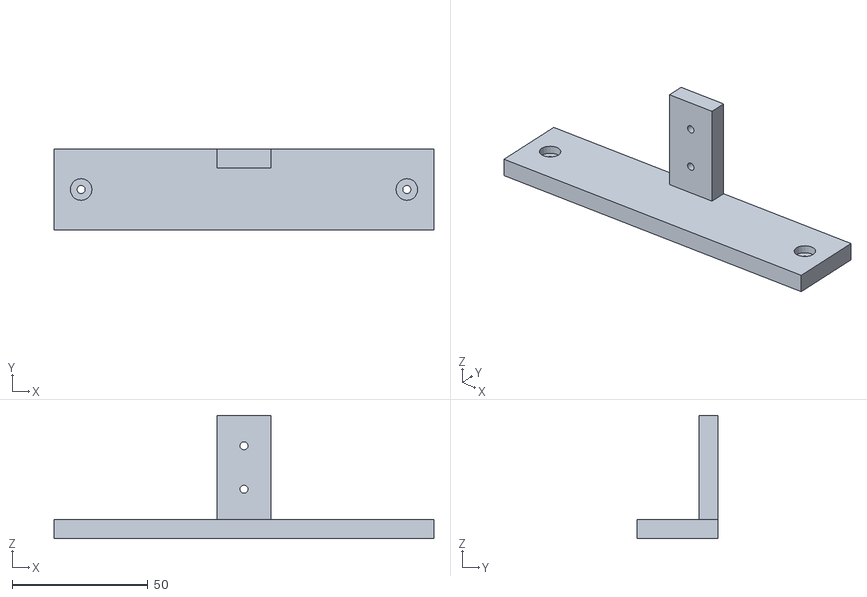
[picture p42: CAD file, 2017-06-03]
models/XYZ/cable_chain/cable_chain_15x30_holder_carriage_bridge.stl
140.0 x 30.0 x 45.5

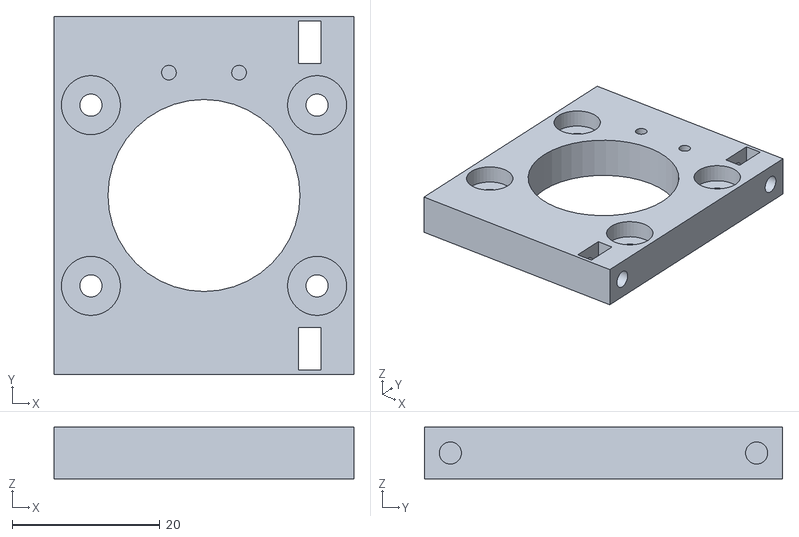
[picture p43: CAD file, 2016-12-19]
models/XYZ/motors_carriages/belt_holder_x/belt_holder_x_fix.stl
40.6 x 48.5 x 7.00

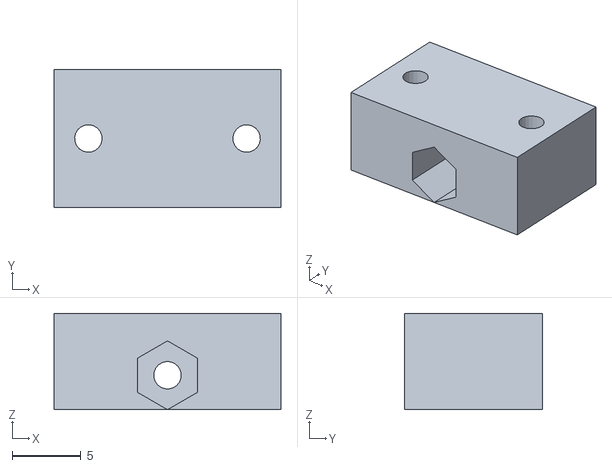
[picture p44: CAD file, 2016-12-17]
models/XYZ/motors_carriages/belt_tensioner/belt_tensioner_bot.stl
16.5 x 10.0 x 7.00

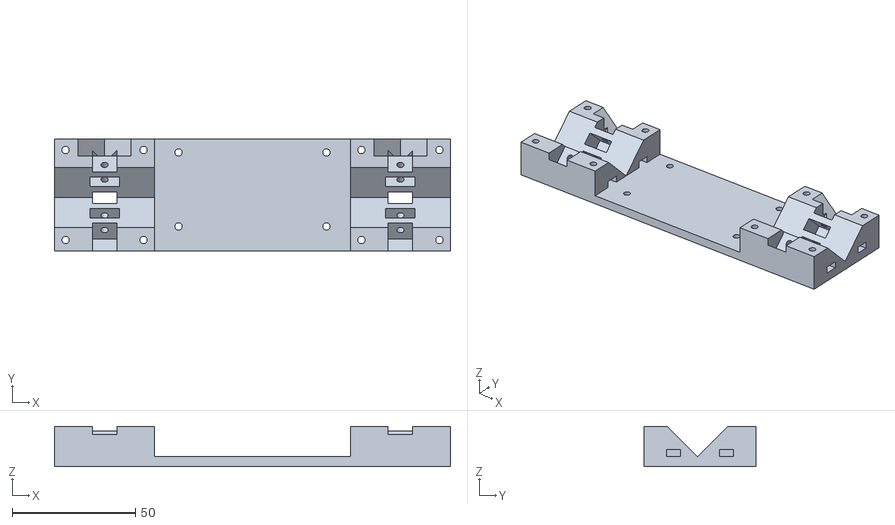
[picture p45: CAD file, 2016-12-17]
models/XYZ/motors_carriages/carriage/carriage_bot_x.stl
160.6 x 45.5 x 16.3

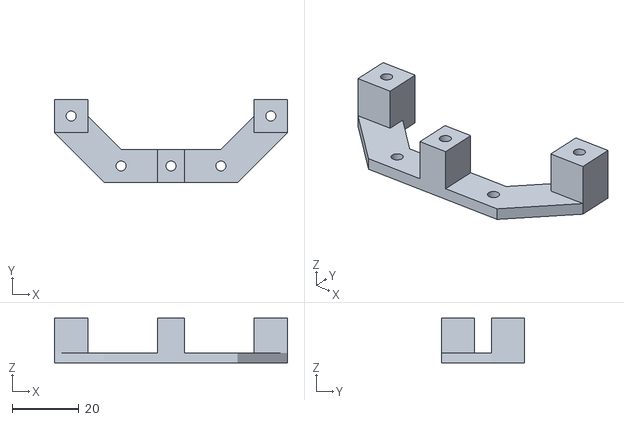
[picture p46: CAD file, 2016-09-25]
models/XYZ/motors_carriages/motor_block/motor_block_pulley_holder.stl
70.0 x 25.0 x 13.5

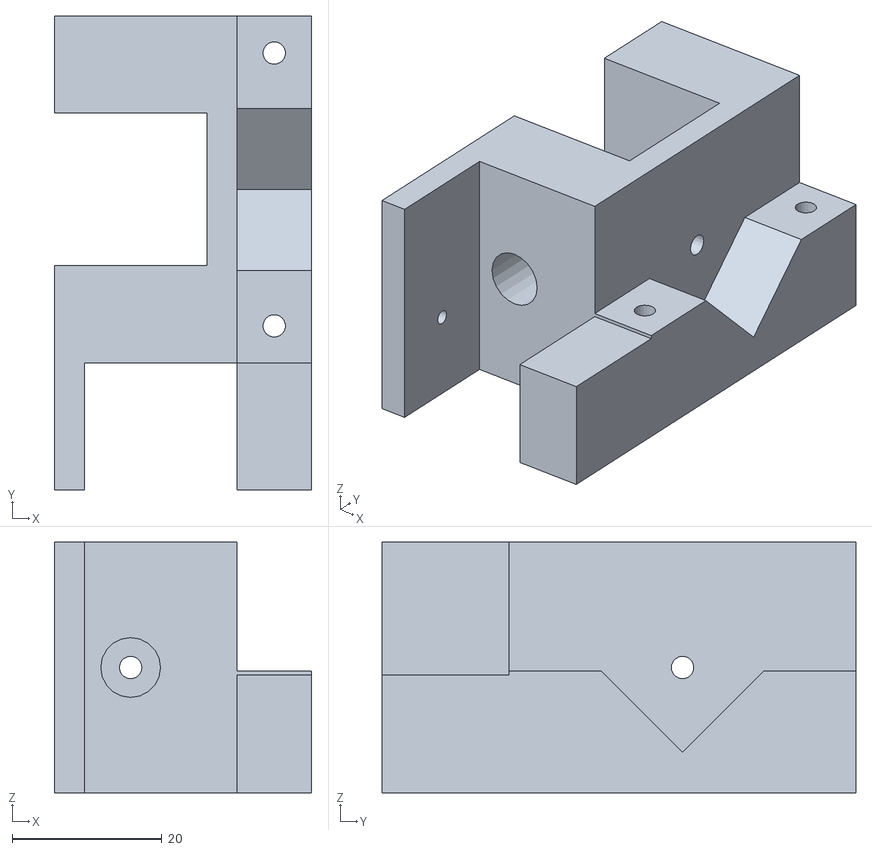
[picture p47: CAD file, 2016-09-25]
models/XYZ/motors_carriages/rod_fix/rod_fix_bot.stl
34.4 x 63.4 x 33.5

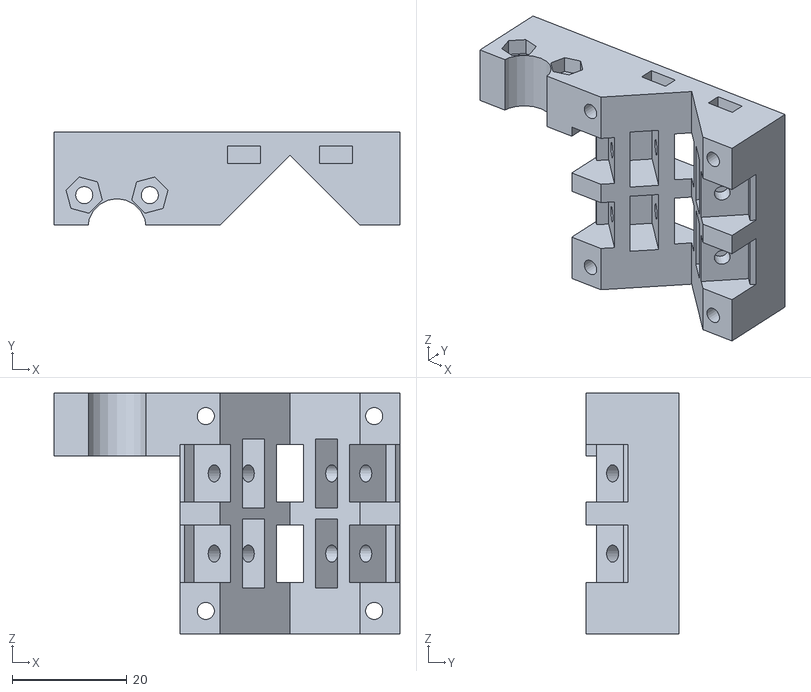
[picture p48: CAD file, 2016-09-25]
models/XYZ/Z/cariage/cariage_z_back.stl
60.4 x 16.3 x 42.0

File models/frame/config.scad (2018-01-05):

$fn=20;

aluminium_extrusion_size = 20.4;
aluminium_extrusion_length = 650;



material_on_rod_length = 40; // the length of material wrapping the rods
material_thickness = 4;

screw_diameter = 3;

screw_diameter_m6 = 6;
nut_diameter_m6 = 11.7;
nut_height_m6 = 5;

reinforcement_3D_size = 15;
reinforcement_2D_size = 15;
reinforcement_2D_unsharp_size = 30;

base_unsharp_size = 10;


// do not touch
screw_height = 100;
reinforcement_3D_margin = 1;
reinforcement_2D_margin = 1;
base_unsharp_margin = 1;


// computed

base_cube_size = aluminium_extrusion_size + material_on_rod_length + material_thickness;
base_cube_offset = (base_cube_size / 2) - (aluminium_extrusion_size / 2) - material_thickness;


module screw() {
    cylinder(r=(screw_diameter / 2), h=screw_height , center=true);
}
// screw

module rod() {
    color([0.7, 0.7, 0.7, 1])
		cube([aluminium_extrusion_size, aluminium_extrusion_length,aluminium_extrusion_size], center=true);
}
// rod

module positioned_aluminium_extrusion_rod_screw_holder(rel_pos, rotation) {
	
	base_border = (aluminium_extrusion_size / 2) + material_on_rod_length;
	
	rotate([0, 90 * rotation, 0])
	translate([0, base_border + rel_pos, 0])
	screw();
}
// positioned_aluminium_extrusion_rod_screw_holder
module positioned_aluminium_extrusion_rod() {
	
	delta = (aluminium_extrusion_length / 2) + (aluminium_extrusion_size / 2) + 1;
	
	translate([0, delta, 0])
	rod();
	
	
	base_border = (aluminium_extrusion_size / 2) + material_on_rod_length;
	
	color([1, 0, 0, 0.7])
	union() {
		positioned_aluminium_extrusion_rod_screw_holder(-10, 0);
		positioned_aluminium_extrusion_rod_screw_holder(-(material_on_rod_length - 10), 0);
		positioned_aluminium_extrusion_rod_screw_holder(-10, 1);
		positioned_aluminium_extrusion_rod_screw_holder(-(material_on_rod_length - 10), 1);
	}
}
//positioned_aluminium_extrusion_rod


module reinforcement_3D() {
	reinforcement_3D_points = [
		[0, 0, 0],
		[reinforcement_3D_size + reinforcement_3D_margin, 0, 0],
		[0, reinforcement_3D_size + reinforcement_3D_margin, 0],
		[0, 0, reinforcement_3D_size + reinforcement_3D_margin],
	];
  
	reinforcement_3D_faces = [
		[0, 1, 2], // x, y plan
		[0, 2, 3], // y, z plan
		[0, 3, 1], // x, z plan
		[1, 3, 2]
	]; 
  
	polyhedron(reinforcement_3D_points, reinforcement_3D_faces);
}
// reinforcement_3D

module reinforcement_2D() {
	reinforcement_2D_width = aluminium_extrusion_size + reinforcement_2D_margin;
	translate([0, 0, -(reinforcement_2D_width / 2)])
    linear_extrude(height=reinforcement_2D_width)
    polygon([
        [0, 0],
        [reinforcement_2D_size + reinforcement_2D_margin, 0],
        [0, reinforcement_2D_size + reinforcement_2D_margin]
    ]);
}
//reinforcement_2D


module base_cube_remove_inner_2D_corner() {
	base_cube_remove_inner_2D_corner_size = material_on_rod_length * 1;
	
	base_cube_remove_inner_2D_corner_offset = (base_cube_remove_inner_2D_corner_size / 2) + (aluminium_extrusion_size / 2) + material_thickness;
	
	reinforcement_2D_offset = (aluminium_extrusion_size / 2) + material_thickness - (reinforcement_2D_margin / 2);
	
	
	base_cube_remove_inner_2D_corner_unsharp_length = aluminium_extrusion_size + (material_thickness * 2) + 1;
	
	base_cube_remove_inner_2D_corner_unsharp_size = reinforcement_2D_unsharp_size * sqrt(2);
	
	base_cube_remove_inner_2D_corner_unsharp_offset = (aluminium_extrusion_size / 2) + material_on_rod_length;
	
	screw_offset = (reinforcement_2D_size + ((material_on_rod_length - material_thickness) * 2 - reinforcement_2D_unsharp_size)) / 4
	+ (aluminium_extrusion_size / 2) + material_thickness;
	
	color([1, 0, 0, 0.7])
	union() {
		difference() {
			translate([0, base_cube_remove_inner_2D_corner_offset, base_cube_remove_inner_2D_corner_offset])
			cube([aluminium_extrusion_size, base_cube_remove_inner_2D_corner_size, base_cube_remove_inner_2D_corner_size], center=true);
			
			translate([0, reinforcement_2D_offset, 		reinforcement_2D_offset])
			rotate([0, -90, 0])
			reinforcement_2D();
		}
		
		
		translate([0, base_cube_remove_inner_2D_corner_unsharp_offset, 		base_cube_remove_inner_2D_corner_unsharp_offset])
		rotate([45, 0, 0])
		cube([base_cube_remove_inner_2D_corner_unsharp_length, base_cube_remove_inner_2D_corner_unsharp_size, base_cube_remove_inner_2D_corner_unsharp_size], center=true);
	
		translate([0, screw_offset, screw_offset])
		rotate([0, 90, 0])
		screw();
	}
}
// base_cube_remove_inner_2D_corner

//base_cube_remove_inner_2D_corner();

module _calibration_screw_m6_test() {
	
	_calibration_rod_test_thickness = 2;
	_calibration_rod_test_size = nut_diameter_m6 + (_calibration_rod_test_thickness * 2);
	
	difference() {
		
		cube([_calibration_rod_test_size, _calibration_rod_test_size, 4], center=true);
		
		cylinder(r=(nut_diameter_m6 / 2), h=50 , $fn=6, center=true);
	}
}
// _calibration_screw_m6_test


module _calibration_rod_test() {
	
	_calibration_screw_test_thickness = 2;
	_calibration_screw_test_size = aluminium_extrusion_size + (_calibration_screw_test_thickness * 2);
	
	difference() {
		
		cube([_calibration_screw_test_size, _calibration_screw_test_size, 4], center=true);
		
		cube([aluminium_extrusion_size, aluminium_extrusion_size, aluminium_extrusion_length], center=true);
	}
}
// _calibration_rod_test
//_calibration_rod_test();
//_calibration_screw_m6_test();

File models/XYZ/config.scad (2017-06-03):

include <../parts/switch.scad>


rod_side = 16;
rod_length = 700;

rod_horizontal_spacing	= 120; // center to center / min 105
rod_vertical_spacing	= 2;

bearing_outer_diameter = 10;
bearing_inner_diameter = 3;
bearing_height = 4;

    // avoid touching this except if you know what's you're doing
    
bearing_holder_spacing_1 = 0.7; // space between bearing flat sides and piece
bearing_holder_spacing_2 = 1; // space between bearing perimeter and piece
bearing_holder_width = 3; // thickness of pieces holding the bearings
bearing_screw_access_size = 10; // the size of the cube to remove to be able to put in place the bearing screw

screw_exceed = 3; // how much you want a screew can exceed in length
    // default M3 screws size
screw_diameter = 3; // the diameter of your screws
    // default M3 nuts size
screws_nuts_side_min = 5.75; // 5.4min
screws_nuts_side_max = 6.55; // default is 6mm but we add some margin
screw_nuts_height = 3; // default is 2.4mm
screws_material_holder_min_size = 3; // the minimum of material arround a screw
screws_attach_length = 10; // the min length of the screew which will attach the 2 pieces

rod_holder_size = 7; // the length of material which will tighten the carriage rods => 10 for Y, 7 for X

rod_piece_spacing = 1; // space between rod and piece
   
pieces_spacing = 1; // the space between the 2 pieces

motor_holder_thickness = 4; // thickness of motor support


/*
    Computed variables for future use
*/

rod_remove_side = rod_side + (rod_piece_spacing * 2);

    // represent the min size of material which should warp a screw
screw_virtual_holder_side = screw_diameter + (screws_material_holder_min_size * 2);

	// represent the area taken by bearings
bearing_virtual_cube_side = (((rod_side / 2) + bearing_outer_diameter + (bearing_height / 2) + bearing_holder_spacing_1 + bearing_holder_width) / sqrt(2)) * 2;

    // the outers screews could touch the rod, so we need to compute an offset
space_rod_outer = (bearing_virtual_cube_side - (rod_remove_side * sqrt(2))) / 2; // the minimum must be screw_virtual_holder_side
echo("space_rod_outer", space_rod_outer);
outer_screw_offset = abs(screw_virtual_holder_side - space_rod_outer);

	// base piece size
base_block_x = rod_horizontal_spacing + (rod_side * sqrt(2)) + (screw_virtual_holder_side * 2);  
base_block_y = bearing_virtual_cube_side + rod_holder_size /*+ screw_virtual_holder_side*/ + outer_screw_offset;
base_block_z = max(bearing_virtual_cube_side, rod_remove_side * sqrt(2) + motor_holder_thickness * 2);


 base_block_remove_x = rod_horizontal_spacing - (rod_side * sqrt(2)) - (screw_virtual_holder_side * 2);
base_block_remove_y = base_block_y;
base_block_remove_z = max(rod_remove_side * sqrt(2), base_block_z - (motor_holder_thickness * 2));


carriage_block_x = (rod_side * sqrt(2)) + (screw_virtual_holder_side * 2);

/*
    RODS
*/

module rod(show_rods) {
    if(show_rods) {
        color([0.7, 0.7, 0.7])
        rotate([45, 0, 0])
        cube([rod_length, rod_side, rod_side], center = true);
    }
}
// draw a rod


module screw(screw_height = 50) {
    cylinder (r=(screw_diameter / 2), h=screw_height , center=true);
}




module base_screw_remove_tighten() {
    
    
    color([1, 0, 0, 0.7])
    union() {
        
        screw_length = base_block_z + 1;
        
        cylinder (r=(screw_diameter / 2), h=screw_length, center=true);
    
        nuts_remove_length = (screw_length / 2) - (screws_attach_length / 2);
    
        translate([0, 0, (screw_length / 2) - (nuts_remove_length / 2)])
        cylinder ($fn = 6, r=(screws_nuts_side_max / 2), h=nuts_remove_length, center=true);
        
        translate([0, 0, -((screw_length / 2) - (nuts_remove_length / 2))])
        cylinder ($fn = 6, r=(screws_nuts_side_max / 2), h=nuts_remove_length, center=true);
    }
}
// base_screw_remove_tighten


/**
	CARRIAGE
**/

module carriage_block_fix_screw(pos_x, pos_y, height = 7) {
	fixation_offset_x = 5;
	fixation_offset_y = 12;
	
	x_offset = (carriage_block_x / 2) - fixation_offset_x;
	y_offset = (base_block_y / 2) - fixation_offset_y;
	
	screw_wacher_diameter = 8;
	screw_wacher_z = 3;
	screw_wacher_z_offset = (height / 2);
	
	translate([(x_offset * pos_x), (y_offset * pos_y), 0])
	union() {
		screw();
		translate([0, 0, screw_wacher_z_offset])
		cylinder (r=(screw_wacher_diameter / 2), h=(screw_wacher_z * 2) , center=true);
	}
}
//carriage_block_fix_screw


module carriage_block_fix(height = 7) {
	carriage_block_fix_screw(+1, +1, height);
	carriage_block_fix_screw(-1, +1, height);
	carriage_block_fix_screw(+1, -1, height);
	carriage_block_fix_screw(-1, -1, height);
}
//carriage_block_fix


/*
    SWITCH
*/

switch_x = 19.8;
switch_y = 11.5;
switch_y_total = 15.3;
switch_z = 6.4;
switch_diameter = 2; // 2.5

module switch() {
	
	//difference() {
		
		union() {
				
			translate([0, (switch_y / 2) - 2.9, 0])
			cube([switch_x, switch_y, switch_z], center = true);
			
			switch_pin_y = switch_y_total - switch_y;
			color([0, 1, 0, 0.7])
			translate([0, -(switch_pin_y / 2) - 2.9 + 0.01, 0])
			cube([switch_x, switch_pin_y, switch_z], center = true);
		}
		
		color([1, 0, 0, 0.7])
		union() {
			translate([-9.5 / 2, 0, 0])
			cylinder (r=(switch_diameter / 2), h=20 , center=true);
			translate([ 9.5 / 2, 0, 0])
			cylinder (r=(switch_diameter / 2), h=20 , center=true);
		}
	//}
}
// ss-5gl

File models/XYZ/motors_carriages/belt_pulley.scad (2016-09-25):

$fn=100;

bearing_outer_diameter = 10.2;
bearing_height = 4;

belt_pulley_inner_diameter_thickness = 1;
belt_pulley_inner_diameter = bearing_outer_diameter + (belt_pulley_inner_diameter_thickness * 2);
belt_pulley_outer_diameter = 18;
belt_pulley_inner_height   = 6.5;
belt_pulley_outer_height   = 9.5;


belt_pulley_border_height  = (belt_pulley_outer_height - belt_pulley_inner_height) / 2;


module belt_pulley_border() {
    color([1, 1, 0, 0.7])
    translate([0, 0, (belt_pulley_outer_height / 2) - (belt_pulley_border_height / 2)])
    cylinder (r1=(belt_pulley_inner_diameter / 2), r2=(belt_pulley_outer_diameter / 2), h=belt_pulley_border_height , center=true);
}



module base_piece() {
    union() {
        color([1, 1, 0, 0.7])
        cylinder (r=(belt_pulley_inner_diameter / 2), h=belt_pulley_outer_height - (belt_pulley_border_height * 2) , center=true);
        belt_pulley_border();
        mirror([0, 0, 1])
        belt_pulley_border();
    }
}

module base_piece_remove() {
    union() {
        // part to remove to be able to insert the bearing
        translate([0, 0, bearing_height / 2])
    color([1, 0, 0, 0.7])
        cylinder (r=(bearing_outer_diameter / 2), h=(bearing_height*2) , center=true);
        
        // part remaining to remove
    color([1, 0, 0, 0.7])
        cylinder (r=(bearing_outer_diameter / 2) - 1, h=belt_pulley_outer_height+ 1, center=true);
    }
}


module _render() {
    difference() {
        base_piece();
        base_piece_remove();
    }
}

    // the bearing
//color([1, 0, 1, 0.7])
//cylinder (r=(bearing_outer_diameter / 2), h=bearing_height, center=true);

_render();

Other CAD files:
models/XYZ/Z/cariage_fix/cariage_fix_part_2.stl
models/XYZ/Z/motor_block/motor_gearbox_adapter.stl
models/XYZ/Z/rod_fix_z/rod_fix_z_top.stl
models/electronics/power_supply/power_strip_fix.stl
models/XYZ/motors_cariages/belt_holder/belt_holder.scad
models/XYZ/Z/cariage/cariage.scad
models/XYZ/Z/cariage/cariage_z_front.stl
models/XYZ/Z/cariage_fix/cariage_fix.scad
models/XYZ/Z/cariage_fix/cariage_fix_part_1.stl
models/XYZ/Z/motor_block/motor_block.scad
models/XYZ/Z/motor_block/motor_block.stl
models/XYZ/Z/motor_block/motor_block_pulley_holder_bot.stl
models/XYZ/Z/motor_block/motor_block_pulley_holder_top.stl
models/XYZ/Z/motor_block/pulley_holder.stl
models/XYZ/Z/rod_fix_z/rod_fix_z.scad
models/XYZ/Z/rod_fix_z/rod_fix_z_bot.stl
models/XYZ/cable_chain/cable_chain.scad
models/XYZ/cable_chain/cable_chain_10x20_holder.scad
models/XYZ/cable_chain/cable_chain_10x20_holder_carriage_1.stl
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

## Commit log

2016-09-25 update bom
2016-09-25 bom ++
2016-09-25 frame ++
2016-09-25 add y_axis
2016-09-25 ++ bom
2016-09-26 doc ++ y axis
2016-09-26 y axis ++
2016-09-26 pulley ++
2016-09-30 finish y axis, start Z
2016-10-09 cariage fix
    [cariage.scad, cariage_fix.scad, cariage_fix_part_1.stl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]
2016-10-20 fix bom
2016-10-22 poer_supply_socket done
    [power_socket.stl, power_supply.scad]
2016-10-25 power supply fix
    [power_supply.scad, power_supply_fix.stl]
2016-12-17 wip x axis parts
    [belt_holder_x.scad, belt_holder_x_bot.stl, belt_holder_x_top.stl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]
2016-12-19 belt holder fix X
    [belt_holder_x.scad, belt_holder_x_fix.stl]
2017-01-05 update doc
    [carriage.scad, foots.scad, foots.stl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]
2017-01-05 review of the Z axis doc
2017-01-09 update X doc
    [belt_holder_x.scad, belt_holder_x_bot.stl, belt_holder_x_fix.stl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]
2017-01-15 update power supply doc + update various TODO
    [power_socket (1).amf]
2017-03-26 add cable chain holder
    [cable_chain.scad, cable_chain_10x20_holder.scad, cable_chain_10x20_holder.stl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]
2017-03-27 wip spindler
    [tool_base.scad]
2017-03-28 spindler block v1
    [spindler.scad, spindler_vacuum.stl, tool_base.scad]
2017-03-29 wip cable chain holder carriage
    [belt_holder_x.scad, cable_chain_10x20_holder.scad, config.scad]
2017-04-02 add new images + add cable chain holder for Y axis + wip cnc tools
2017-04-02 update power supply doc
2017-04-02 update home page doc
    [belt_holder_x.scad, cable_chain_10x20_holder.scad, cable_chain_10x20_holder_carriage_1.stl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]
2017-04-09 add sprindler base
    [carriage.scad, spindle_vaccum_test.scad, spindler.scad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]
2017-04-09 add cable chain Y doc
2017-04-09 add spindler doc
2017-05-29 wip cable chain 30x15
    [cable_chain_15x30_holder.scad, cable_chain_15x30_holder_frame.stl]
2017-05-29 wip cable chain 15x30 on X cariage
    [cable_chain_15x30_holder.scad, config.scad]
2017-05-30 cable_chain_15x30_holder_carriage v01 done
    [cable_chain_15x30_holder.scad]
2017-06-03 cable chain for X axis
    [cable_chain_15x30_holder.scad, cable_chain_15x30_holder_carriage_attach.stl, cable_chain_15x30_holder_carriage_bridge.stl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]
2017-06-03 add table of content on X axis
2017-06-03 wip extruder
    [extruder.scad]
2017-06-05 extruder experimental
    [base_part (1).amf, base_part.stl, extruder.scad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]
2017-07-10 wip diamond extruder
    [base_part_all.stl, base_part_bot.stl, base_part_top.stl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]
2018-01-01 wip top cover of diamond hot end
    [diamon_hotend.scad, diamond_hotend.scad, e3d_v6.scad]
2018-01-03 wip diamond hotend
    [BLTouch.stl, diamon_hotend.scad, diamond_hotend.scad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]
2018-01-05 v1 of diamond extruder
    [config.scad, corder_3d_smooth_slide.stl, corner_3d.scad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]
2018-01-07 extrdudeur print
    [diamond_hotend.scad, diamond_hotend_base.stl]
2018-01-21 add smooth slide for X cable chain
